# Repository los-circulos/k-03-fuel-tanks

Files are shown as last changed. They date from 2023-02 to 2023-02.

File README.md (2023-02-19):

# k-03 fuel tanks

Templates for copper sheet tanks and 3d printable plastic tank models

## copper sheet tanks

- SVG vector format plans for cutting sheets
- There are wooden templates to bend the sheets

Apart from the general SVG file, a separate cut files are included with each design, ready to be burn cut (one for ply, and another optimized for balsa 100mm wide boards).

### Material
3mm plywood or balsa.
- Plywood makes a nice template to precisely bend copper.
- Balsa would have to be glassed from the inside and used as the fuel tank itself (NOTE: it will have ~10% less capacity like this, the exact difference varies based on the chosen design.

### Designs
- K 9 - 30mm wide, narrow top angle "doghouse".
- fatboy 10 - 38mm wide, low profile tank
- stunt 11 - 26mm wide, slim but tall "basic" design

### Files provided
For each design (substitute k_9 with preferred design name):
- tank-k_9-45cc.svg - main file for a 45cc tank
- tank-k_9-45cc-cut.svg - cut file for plywood
- tank-k_9-45cc-cut-100.svg - cut file for balsa (100mm wide board)

## 3d printable models

- STF model files of various tank sizes
- legs with oval openings for adjustable height
- separate retainer design file

### Material
Currently I used polypropilene PP which resists most chemicals. For the retainers, I use PET.
- up to 125% overfill
- 0.16mm layer height, 0.4mm line width
- lower temperature for the top nipples (use postprocess script)

### Designs

- NO8 plumbing, direct tube nipple exits, no internal tubes
- fatboy low 6.5-30
- fatboy 8-41
- fatboy 8-66
- stunt 8-65
- stunt 10-100

@los.circulos
instagram.com/los.circulos
github.com/los-circulos
#controlline #vuelocircular #uコン #opensource

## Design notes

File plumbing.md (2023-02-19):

Plumbing designs
===

It is difficult to know about a closed tank what it has inside. So, I'm numbering the plumbing design as the following. It is rather a memo to me than useful info.

Note that K-9, Fatboy-10, Stunt-11 etc are tank vessel designs. N°x is plumbing design and could be matched with any vessel design.

 - N°1 - plain stunt tank with straight feed pipe
 - N°2 - simple uniflow tank, feed exits on the spine halfway
 - N°3 - experimental tank with connections to a secondary tank. Similar to N°2 but on the bottom has 2 more connections. One full height one only to the bottom.
 - N°4 - experimental tank made of balsa, carbon tubes, and ciano inside. The cyano covering didn't work out.
 - N°5 - uniflow tank with a no-air brass filter ("syntherized") inside
 - N°6 - plain stunt tank but with a no-air brass filter inside
 - N°7 - uniflow tank with less internal tubing, for 3D printing. Feed and breath have small tubes inserted for fuel hose connection, and overflow tube is inserted from the bottom. 
 - N°8 - uniflow tank without any internal tubing, for 3D printing. Feed, breathe and overflow have small, printed nipples. Overflow is on top, but fuel level is clearly visible (PP polypropilene). Also thes have a small baffle volume, with an inclined baffle plate

Model identification
---

Then, each tank built has its model identification as:

    N°x{.y}-z
      |  |  |
      |  |  └- capacity of tank, in ccm
      |  └--- optional, number of baffle plates. Big tanks made of thin copper might have more than one baffle. Some tanks don't have baffle, then this number and dot are omitted
      └----- model number as per list above

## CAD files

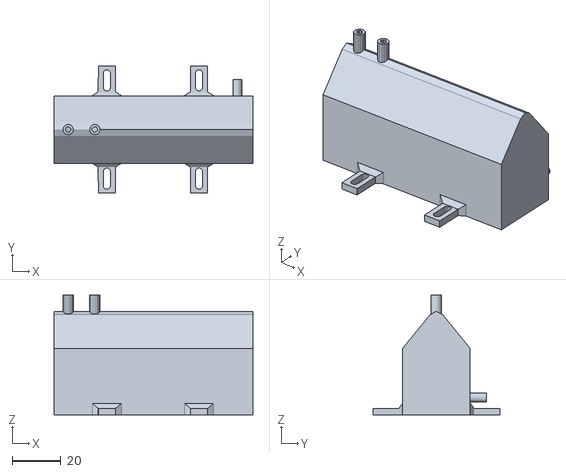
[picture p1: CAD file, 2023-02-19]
3dprint/stunt_8-65-no8.stl
82.0 x 52.5 x 49.3

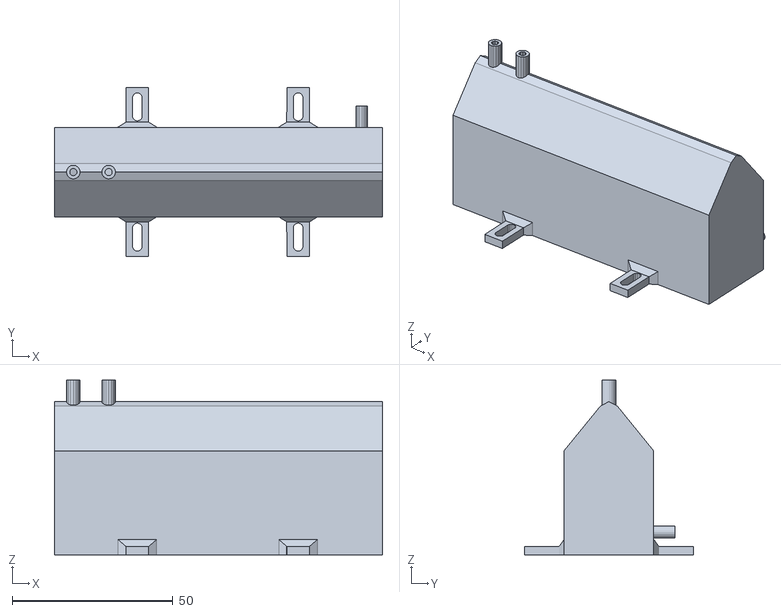
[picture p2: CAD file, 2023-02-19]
3dprint/stunt_10-100-no8.stl
102.0 x 52.5 x 54.3

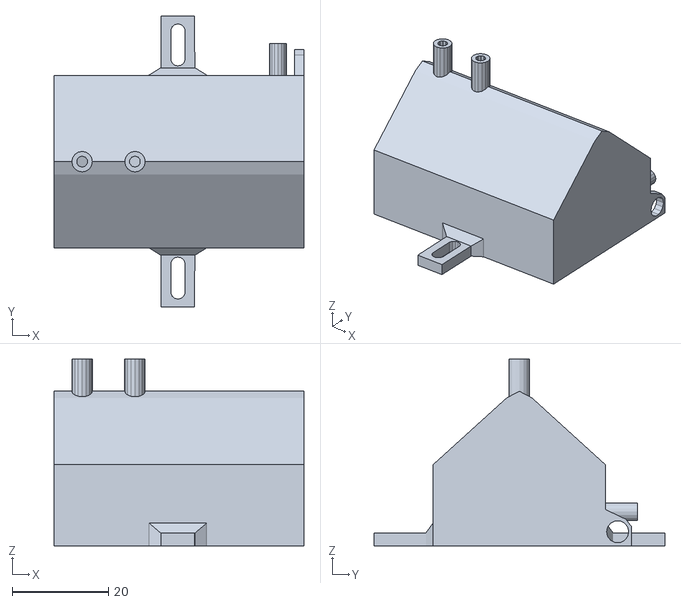
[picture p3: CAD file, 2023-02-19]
3dprint/with tube holder/fatboy_8-41-no8-holder.stl
52.0 x 60.5 x 38.8

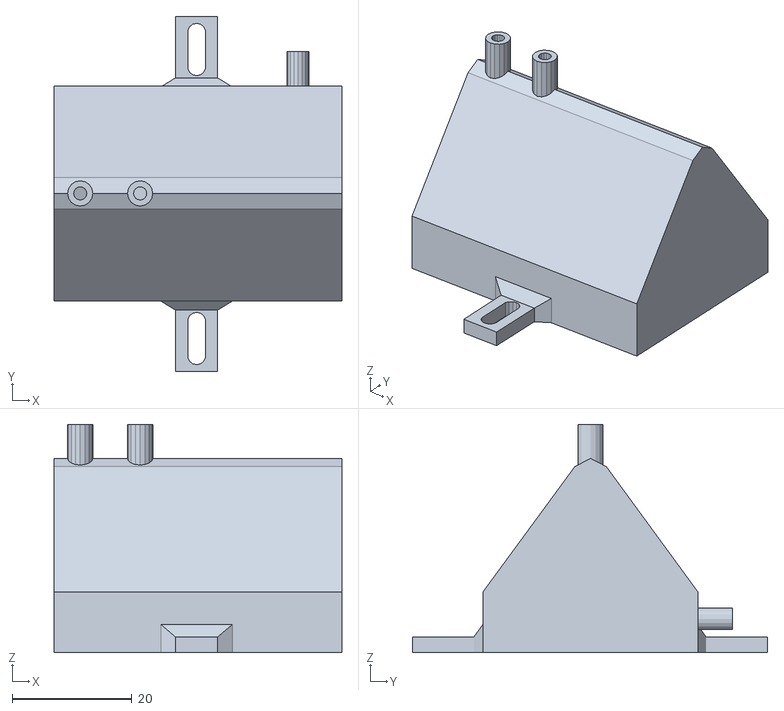
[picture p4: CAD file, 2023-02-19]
3dprint/fatboy_low65-31-no8.stl
48.0 x 59.2 x 38.1

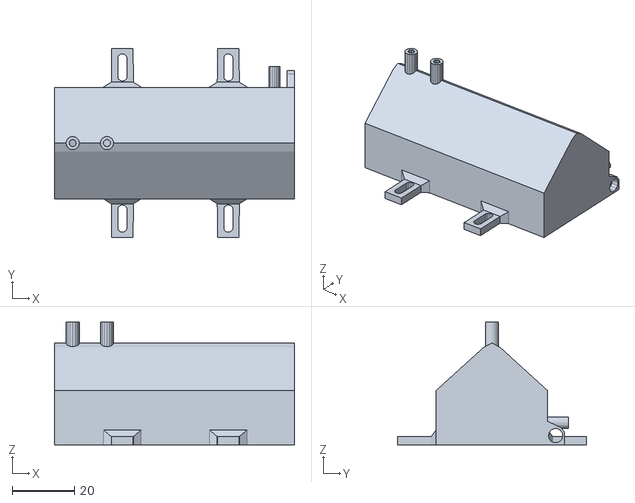
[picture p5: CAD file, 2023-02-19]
3dprint/with tube holder/fatboy_8-66-no8-holder.stl
77.0 x 60.5 x 39.3

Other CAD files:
3dprint/with tube holder/stunt_8-65-no8-holder.stl
3dprint/with tube holder/stunt_10-100-no8-holder.stl
3dprint/fatboy_8-41-no8.stl
3dprint/fatboy_8-66-no8.stl
3dprint/with tube holder/fatboy_low65-31-no8-holder.stl
3dprint/NO8 tanks.blend
